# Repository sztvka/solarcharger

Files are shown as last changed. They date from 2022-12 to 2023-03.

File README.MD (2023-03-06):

# SolarCharger
  
This project is my first shot at programming real-time systems featuring multiple tasks. I wanted to create a dual axis solar tracker that's reliable in terms of hardware and software in the field where most of the similar projects run on a breadboard with an Arduino.
The device is able to:
- Track the sun in two axis
- Charge a Lithium-Ion Battery with current limit and overvoltage protection
- Display a web UI with real-time status of the device
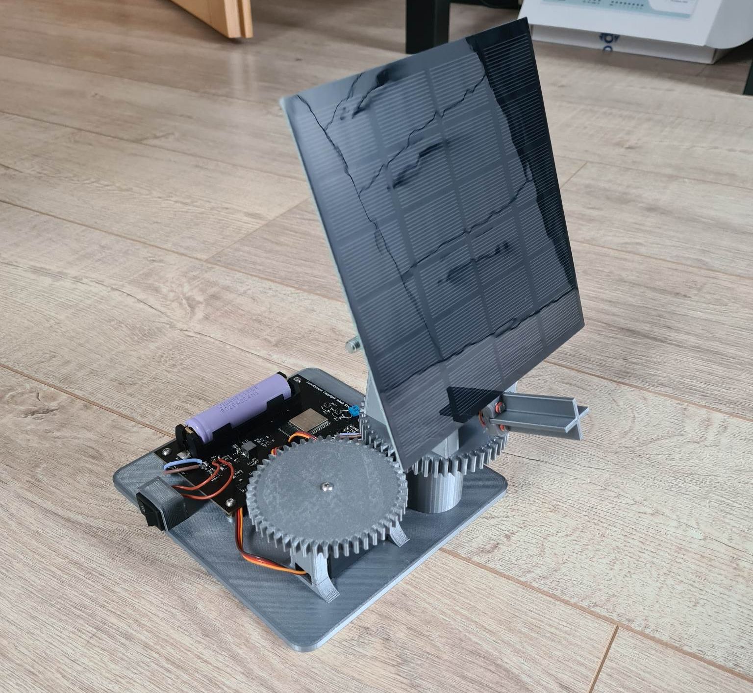
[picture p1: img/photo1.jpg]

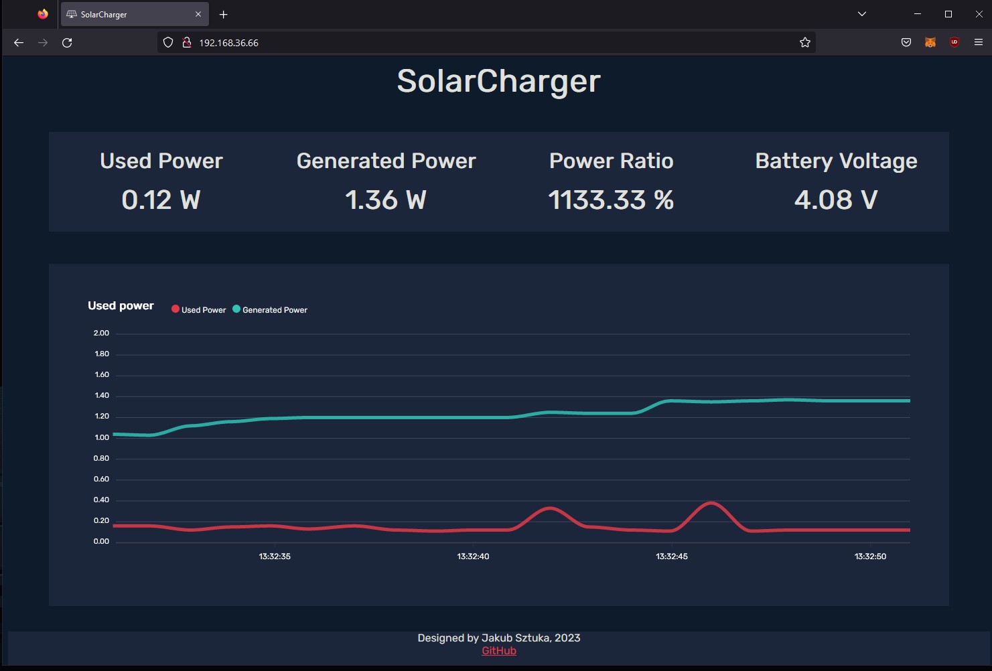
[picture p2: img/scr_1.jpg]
webUI Web UI


## Hardware

### Mechanical
The mechanical design is a remix of the [Dual Axis Solar Tracker](https://www.thingiverse.com/thing:53321) by [OpenSourceClassroom](https://www.thingiverse.com/opensourceclassroom/designs). My updated design fixes some major mechanical issues apparent in the original design, mainly related to poor alignment of the two axis. In my new design, the pan axis is kept aligned with bearings, the gears are screwed on instead of being plastic welded and my design features proper cable management with strain relief.  
Required materials for assembly:
- Printed parts
- M4x10mm Screws
- M4x20mm Screws
- M3x6mm Screws
- 6001 Bearing (I recommend opening it up and removing the grease inside to decrease friction)
- M3 standoffs (Optional, extra space under the pcb allows cable management)
- M6x100mm threaded rod with two M6 nuts
- MG-996R Servo (pan)
- MG90S or SG90 Servo (tilt)
- Cables (silicone insulation is optimal)
- Cable conduit

### Electronics
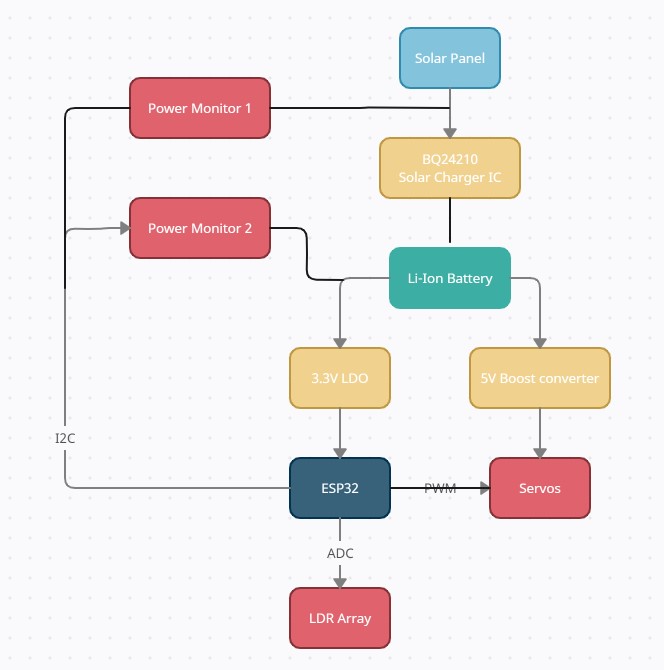
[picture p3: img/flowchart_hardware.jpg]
Hardware flowchart
  
Everything is placed onto a custom pcb. For more details refer to schematics and kicad files in the repository. This design uses a 3W solar panel.

## Software
The code is written in ESP-IDF with FreeRTOS and is designed to run on an ESP32. 

## Compiling

#### Prerequisites
 - [ESP32 Toolchain](https://docs.espressif.com/projects/esp-idf/en/latest/esp32/get-started/index.html#step-2-set-up-the-toolchain)
 - Python interpreter

#### Steps
1. Clone the repository `git clone https://github.com/sztvka/solarcharger.git`
2. Make sure your ESP-IDF path is set correctly and `idf.py` is resolvable
3. Install the required python packages `pip install rjsmin css_html_js_minify`
4. Configure your install in `config_default.h` file
5. Run the `compile_extras.py` script to setup the web UI (this will minify web files and set your config for compiling)
6. Run `idf.py build` to compile the project
7. Flash the device with `idf.py -p (PORT) flash`

## Extra media



https://user-images.githubusercontent.com/47701797/213793889-40177bec-c784-479d-9bc1-420ded0e9b07.mp4

## License

This project is licensed under the Creative Commons Attribution Share Alike 4.0 International - see the [LICENSE](LICENSE) file for details  
cc

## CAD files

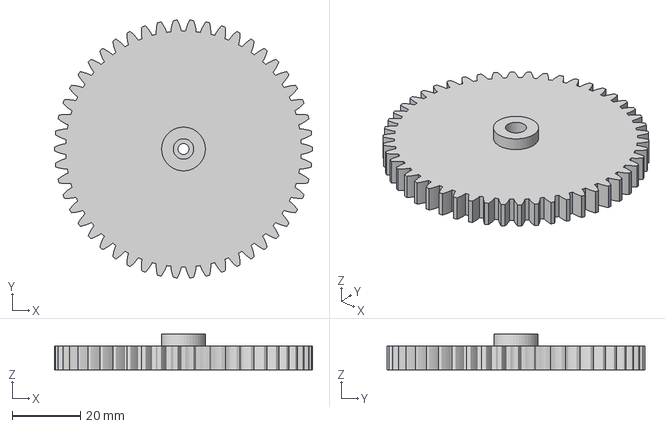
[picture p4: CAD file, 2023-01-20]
3d_models/Pan Gear.3mf
75.4 x 75.3 x 10.5 mm

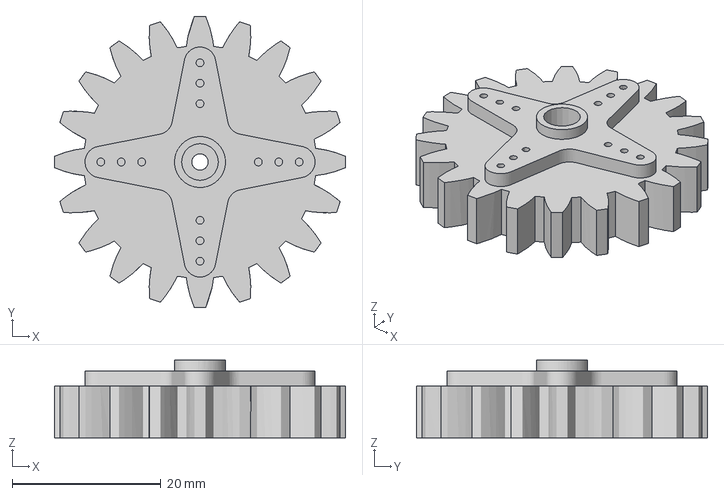
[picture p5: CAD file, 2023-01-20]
3d_models/Tilt Gear.3mf
39.2 x 39.2 x 10.5 mm

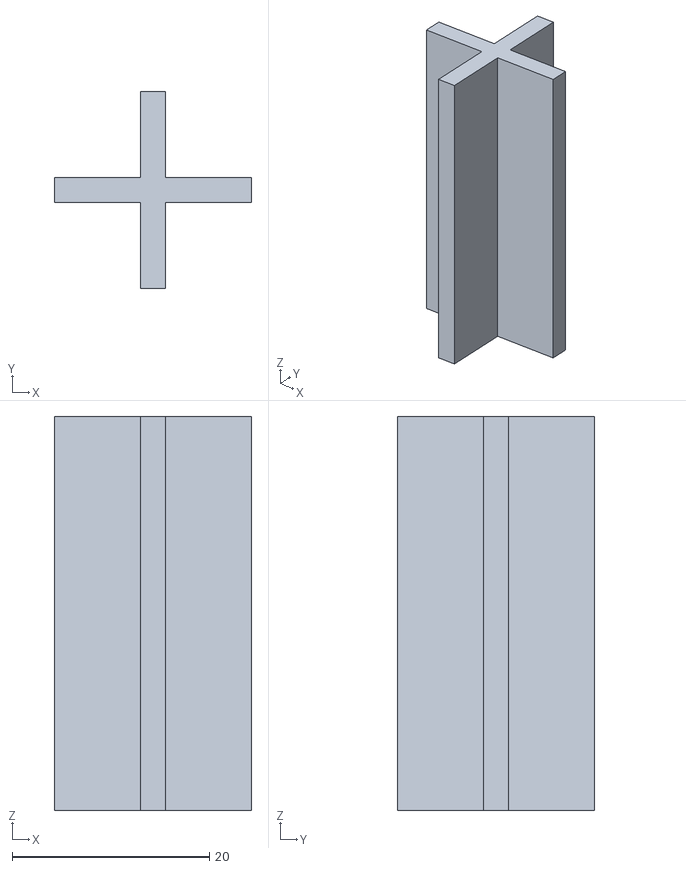
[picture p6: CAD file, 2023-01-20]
3d_models/LDR_Divider.stl
20.0 x 20.0 x 40.0

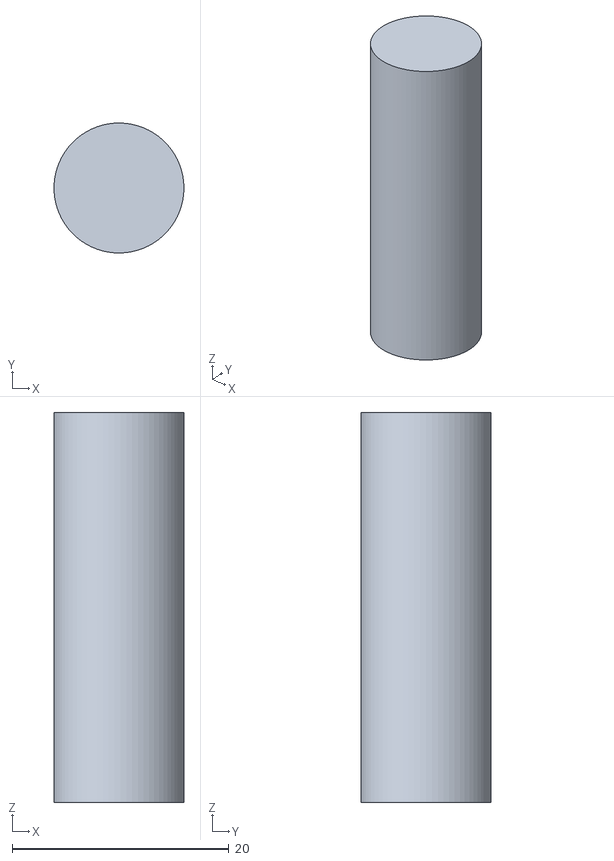
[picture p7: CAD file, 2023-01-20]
3d_models/Base_Gear_Shaft.stl
12.0 x 12.0 x 36.0

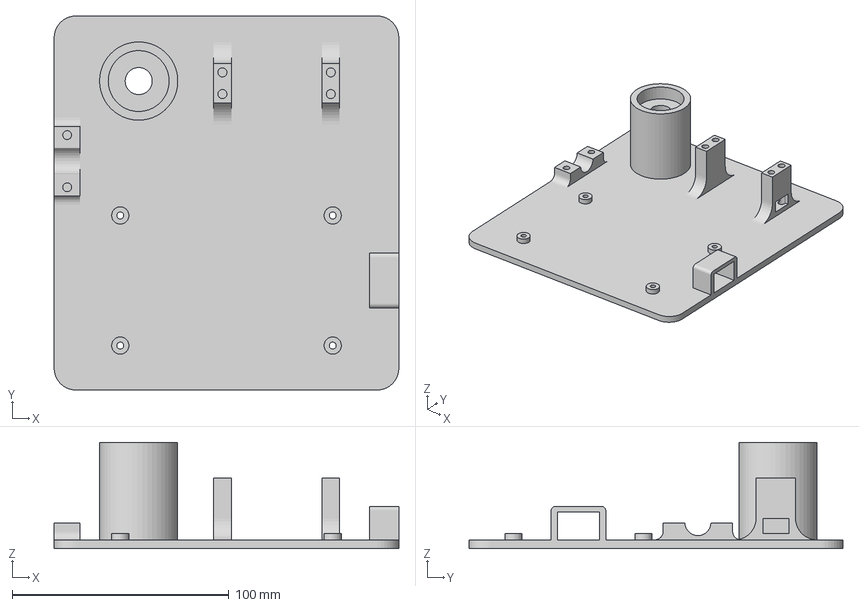
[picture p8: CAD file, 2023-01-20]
3d_models/Base.3mf
159.0 x 172.5 x 49.0 mm

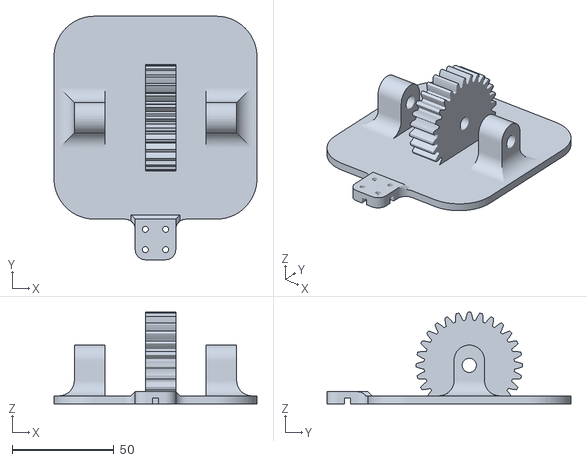
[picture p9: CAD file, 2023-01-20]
3d_models/Panel_Bracket.stl
100.0 x 120.0 x 45.2

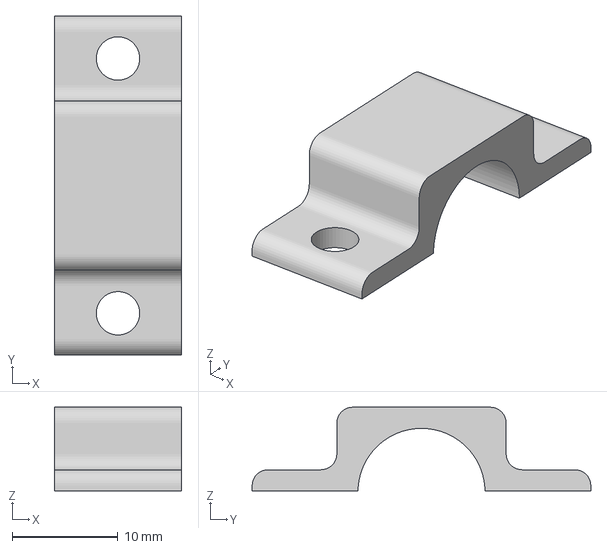
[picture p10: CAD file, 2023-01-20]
3d_models/Cable clip.3mf
12.0 x 32.0 x 7.90 mm

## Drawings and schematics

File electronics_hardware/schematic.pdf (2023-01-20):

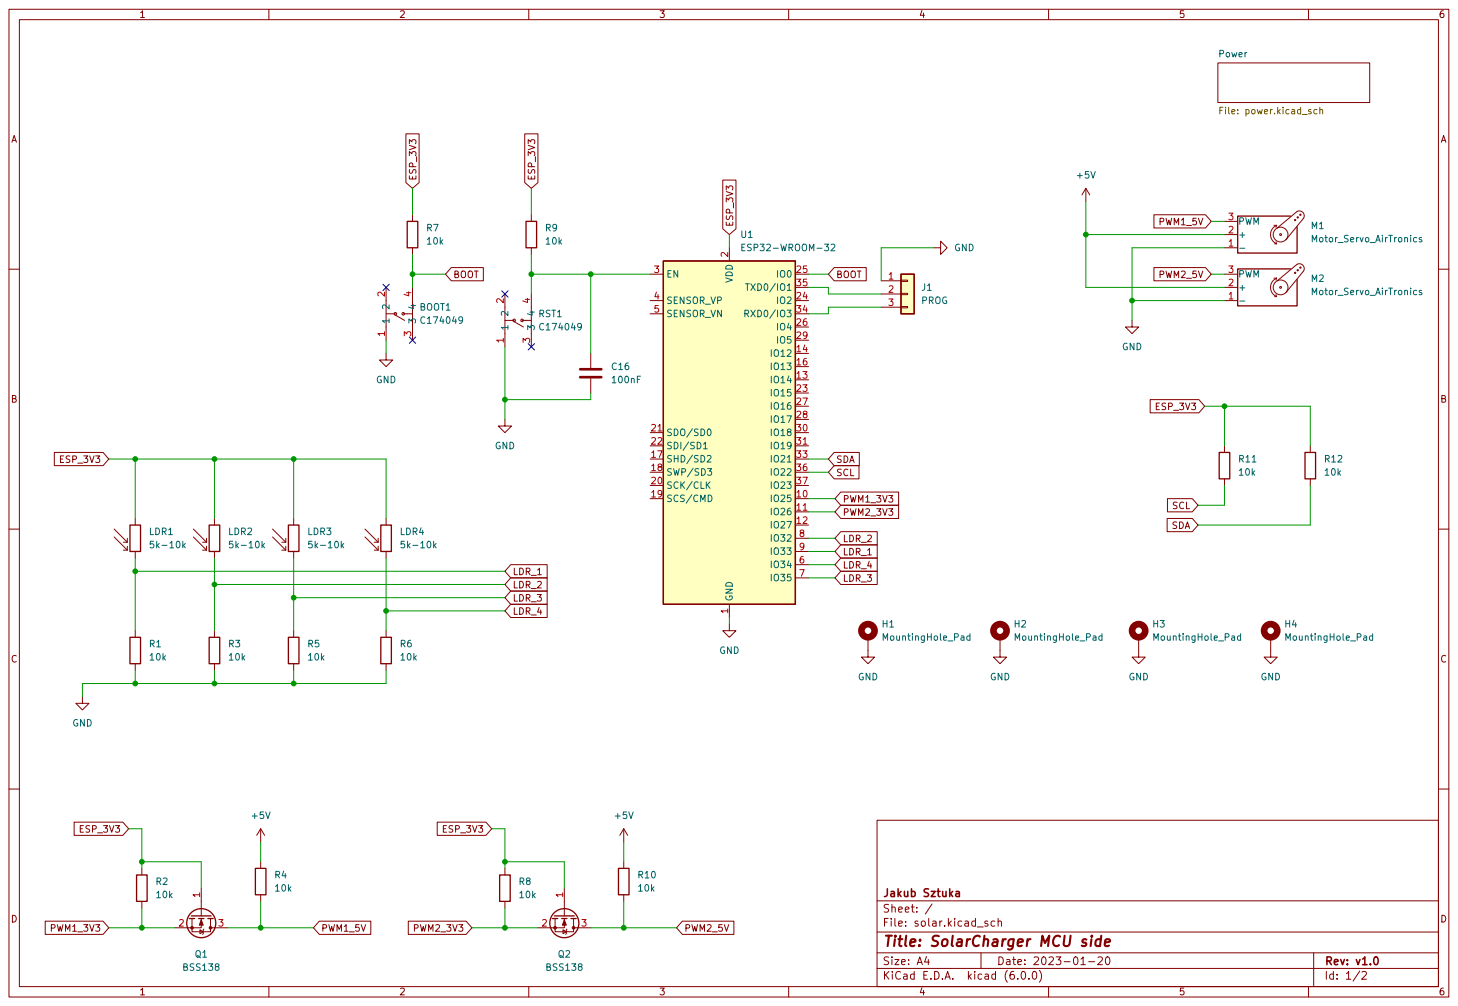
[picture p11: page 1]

2 SCK/CLK 20 SDO/SD0 21 SDI/SD1 22

File: solar.kicad_sch Sheet: / Jakub Sztuka

Id: 1/2 Title: SolarCharger MCU side

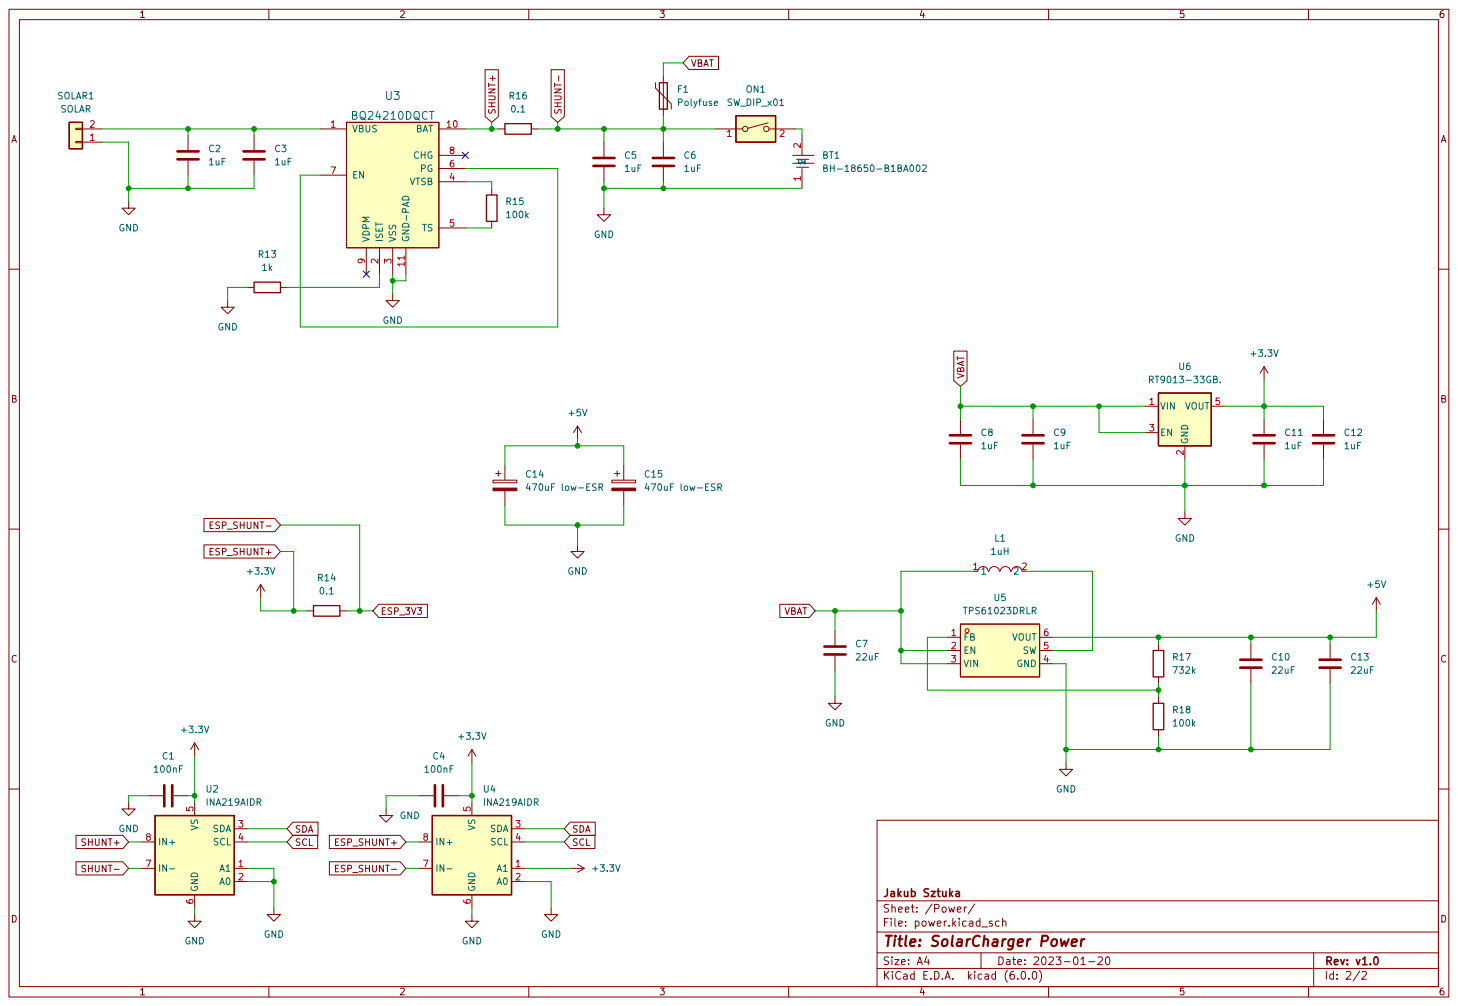
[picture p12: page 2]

3 VTSB 4 TS 5 PG 6 EN 7 CHG 8 VDPM

File: power.kicad_sch Sheet: /Power/ Jakub Sztuka GND

Id: 2/2 Title: SolarCharger Power

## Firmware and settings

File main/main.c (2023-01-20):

#include <sys/cdefs.h>
#include <stdio.h>
#include <freertos/FreeRTOS.h>
#include <freertos/task.h>
#include <ina219.h>
#include <string.h>
#include <esp_log.h>
#include <assert.h>
#include <wifi.h>
#include <iot_servo.h>
#include "driver/adc.h" //deprecated change in the future
#include "esp_adc_cal.h"


#define I2C_PORT 0

#define I2C_SCL 22
#define I2C_SDA 21


// LDR1 33  top left
// LDR2 32  top right
// LDR3 35  bottom left
// LDR4 34  bottom right


#define LDR1 ADC_CHANNEL_4
#define LDR2 ADC_CHANNEL_5
#define LDR3 ADC_CHANNEL_6
#define LDR4 ADC_CHANNEL_7

#define ADC_SAMPLE_SIZE 64

static const adc_bits_width_t width = ADC_WIDTH_BIT_12;
static esp_adc_cal_characteristics_t *ldr_adc_chars;

#define SERVO_1 25
#define SERVO_2 26

#define LDR_DIFF_MOVE_TRESHOLD 100

const uint8_t INA219_1_ADDR = 0x40; //solar
const uint8_t INA219_2_ADDR = 0x44; //esp32

int servo1_angle = 90;
int servo2_angle = 179;

#define SHUNT_MOHM 100
#define MAX_CUR 1


servo_config_t servo_cfg = {
    .max_angle = 180,
    .min_width_us = 500,
    .max_width_us = 2500,
    .freq = 50,
    .timer_number = LEDC_TIMER_0,
    .channels = {
        .servo_pin = {
            SERVO_1,
            SERVO_2,
        },
        .ch = {
            LEDC_CHANNEL_0,
            LEDC_CHANNEL_1,
        },
    },
    .channel_number = 2,
} ;



void ina_measure(void *addr)
{
    TaskHandle_t cur = xTaskGetCurrentTaskHandle();
    char * name = pcTaskGetName(cur);
    ina219_t dev;
    memset(&dev, 0, sizeof(ina219_t));
    uint8_t *address = addr;
    assert(SHUNT_MOHM > 0);
    ESP_ERROR_CHECK(ina219_init_desc(&dev, *address, I2C_PORT, I2C_SDA, I2C_SCL));
    ESP_ERROR_CHECK(ina219_init(&dev));
    ESP_ERROR_CHECK(ina219_configure(&dev, INA219_BUS_RANGE_16V, INA219_GAIN_0_125,
            INA219_RES_12BIT_1S, INA219_RES_12BIT_1S, INA219_MODE_CONT_SHUNT_BUS));

    ESP_ERROR_CHECK(ina219_calibrate(&dev, (float)MAX_CUR, (float)SHUNT_MOHM / 1000.0f));

    float bus_voltage, current, power;

    while (1)
    {
        ESP_ERROR_CHECK(ina219_get_bus_voltage(&dev, &bus_voltage));
        ESP_ERROR_CHECK(ina219_get_current(&dev, &current));
        ESP_ERROR_CHECK(ina219_get_power(&dev, &power));


        if(strcmp(name, "INA219_1")==0) setINA219_1(bus_voltage, current*1000, power*1000); 
        if(strcmp(name, "INA219_2")==0) setINA219_2(bus_voltage, current*1000, power*1000); 
        vTaskDelay(pdMS_TO_TICKS(500));
    }
}



//servo 1 prawo lewo
//sevo 2 gora dol
//servo 2 po odwrocie dol gora


//wieksze od 0 ma isc w prawo
void adjustServos(int diff_vert, int diff_hor){
    if(abs(diff_vert)>=LDR_DIFF_MOVE_TRESHOLD){
        if(diff_vert>0 && servo2_angle>89) servo2_angle-=2;
        else if(diff_vert<0 && servo2_angle<179) servo2_angle+=2;
        iot_servo_write_angle(LEDC_LOW_SPEED_MODE, 1, (float)servo2_angle);
    }
    if(abs(diff_hor)>=LDR_DIFF_MOVE_TRESHOLD){
        if(diff_hor>0 && servo1_angle<179) servo1_angle+=2;
        else if(diff_hor<0 && servo1_angle>1) servo1_angle-=2;
        iot_servo_write_angle(LEDC_LOW_SPEED_MODE, 0, (float)servo1_angle);
    }
}


static void check_adc_efuse(void)
{
    if (esp_adc_cal_check_efuse(ESP_ADC_CAL_VAL_EFUSE_TP) == ESP_OK) {
        printf("ADC eFuse Two Point: Supported\n");
    } else {
        printf("ADC eFuse Two Point: NOT supported\n");
    }
    //Check Vref is burned into eFuse
    if (esp_adc_cal_check_efuse(ESP_ADC_CAL_VAL_EFUSE_VREF) == ESP_OK) {
        printf("ADC eFuse Vref: Supported\n");
    } else {
        printf("ADC eFuse Vref: NOT supported\n");
    }
}


static void print_char_val_type(esp_adc_cal_value_t val_type)
{
    if (val_type == ESP_ADC_CAL_VAL_EFUSE_TP) {
        printf("ADC Characterized using Two Point Value\n");
    } else if (val_type == ESP_ADC_CAL_VAL_EFUSE_VREF) {
        printf("ADC Characterized using eFuse Vref\n");
    } else {
        printf("ADC Characterized using Default Vref\n");
    }
}




void ldr_setup(){
    check_adc_efuse();

    adc1_config_width(width);
    adc1_config_channel_atten(LDR1, ADC_ATTEN_DB_11);
    adc1_config_channel_atten(LDR2, ADC_ATTEN_DB_11);
    adc1_config_channel_atten(LDR3, ADC_ATTEN_DB_11);
    adc1_config_channel_atten(LDR4, ADC_ATTEN_DB_11);
    ldr_adc_chars = calloc(1, sizeof(esp_adc_cal_characteristics_t));
    esp_adc_cal_value_t val_type = esp_adc_cal_characterize(ADC_UNIT_1, ADC_ATTEN_DB_11, width, 1100, ldr_adc_chars);
    print_char_val_type(val_type); 
}

_Noreturn void ldr_read(){
    iot_servo_write_angle(LEDC_LOW_SPEED_MODE, 0, (float)servo1_angle);
    iot_servo_write_angle(LEDC_LOW_SPEED_MODE, 1, (float)servo2_angle);
    while(1){
        uint32_t ldr_raw_reading[4] = {0};
        uint32_t ldr_voltage[4] = {0};
        for (int i = 0; i<ADC_SAMPLE_SIZE; i++){
            ldr_raw_reading[0] += adc1_get_raw((adc1_channel_t)LDR1);
            ldr_raw_reading[1] += adc1_get_raw((adc1_channel_t)LDR2);
            ldr_raw_reading[2] += adc1_get_raw((adc1_channel_t)LDR3);
            ldr_raw_reading[3] += adc1_get_raw((adc1_channel_t)LDR4);
        };
        
        for(int i = 0; i<4; i++){
            ldr_raw_reading[i] /= ADC_SAMPLE_SIZE;
            ldr_voltage[i] = esp_adc_cal_raw_to_voltage(ldr_raw_reading[i], ldr_adc_chars);
        };


    int avg_top = (int)(ldr_voltage[0] + ldr_voltage[1]) / 2;
    int avg_bot = (int)(ldr_voltage[2] + ldr_voltage[3]) / 2;
    int avg_left = (int)(ldr_voltage[0] + ldr_voltage[2]) / 2;
    int avg_right = (int)(ldr_voltage[1] + ldr_voltage[3]) / 2;



    int diff_vertical = avg_top-avg_bot; //  positive: top is brighter   negative: bottom is brighter
    int diff_horizontal = avg_left-avg_right; //positive left is brighter   negative right is brighter


   
    adjustServos(diff_vertical, diff_horizontal);
    vTaskDelay(pdMS_TO_TICKS(100));
    }
}


void app_main()
{
    ESP_ERROR_CHECK(i2cdev_init());

    wifi_init();
    setINA219_1(0.1,0.1,0.1);
    setINA219_2(0.2,0.2,0.2);
    xTaskCreate(ina_measure, "INA219_1", configMINIMAL_STACK_SIZE * 8, (void*)&INA219_1_ADDR, 5, NULL);
    xTaskCreate(ina_measure, "INA219_2", configMINIMAL_STACK_SIZE * 8, (void*)&INA219_2_ADDR, 5, NULL);
    iot_servo_init(LEDC_LOW_SPEED_MODE, &servo_cfg);
    ldr_setup();
    xTaskCreate(ldr_read, "ADC", configMINIMAL_STACK_SIZE*8, NULL, 4, NULL);

}

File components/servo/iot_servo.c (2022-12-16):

// Copyright 2020 Espressif Systems (Shanghai) Co. Ltd.
//
// Licensed under the Apache License, Version 2.0 (the "License");
// you may not use this file except in compliance with the License.
// You may obtain a copy of the License at
//
//     http://www.apache.org/licenses/LICENSE-2.0
//
// Unless required by applicable law or agreed to in writing, software
// distributed under the License is distributed on an "AS IS" BASIS,
// WITHOUT WARRANTIES OR CONDITIONS OF ANY KIND, either express or implied.
// See the License for the specific language governing permissions and
// limitations under the License.

#include "esp_log.h"
#include "esp_err.h"
#include "driver/ledc.h"
#include "iot_servo.h"
#include <config.h>

#define SERVO_CHECK(a, str, ret_val) \
    if (!(a)) { \
        ESP_LOGE(TAG,"%s(%d): %s", __FUNCTION__, __LINE__, str); \
        return (ret_val); \
    }

#define SERVO_LEDC_INIT_BITS LEDC_TIMER_10_BIT
#define SERVO_FREQ_MIN       50
#define SERVO_FREQ_MAX       400

static uint32_t g_full_duty = 0;
static servo_config_t g_cfg[LEDC_SPEED_MODE_MAX] = {0};

static uint32_t calculate_duty(ledc_mode_t speed_mode, float angle)
{
    float angle_us = angle / g_cfg[speed_mode].max_angle * (g_cfg[speed_mode].max_width_us - g_cfg[speed_mode].min_width_us) + g_cfg[speed_mode].min_width_us;
    ESP_LOGD(TAG, "angle us: %f", angle_us);
    uint32_t duty = (uint32_t)((float)g_full_duty * (angle_us) * g_cfg[speed_mode].freq / (1000000.0f));
    return duty;
}

static float calculate_angle(ledc_mode_t speed_mode, uint32_t duty)
{
    float angle_us = (float)duty * 1000000.0f / (float)g_full_duty / (float)g_cfg[speed_mode].freq;
    angle_us -= g_cfg[speed_mode].min_width_us;
    angle_us = angle_us < 0.0f ? 0.0f : angle_us;
    float angle = angle_us * g_cfg[speed_mode].max_angle / (g_cfg[speed_mode].max_width_us - g_cfg[speed_mode].min_width_us);
    return angle;
}

esp_err_t iot_servo_init(ledc_mode_t speed_mode, const servo_config_t *config)
{
    esp_err_t ret;
    SERVO_CHECK(NULL != config, "Pointer of config is invalid", ESP_ERR_INVALID_ARG);
    SERVO_CHECK(config->channel_number > 0 && config->channel_number <= LEDC_CHANNEL_MAX, "Servo channel number out the range", ESP_ERR_INVALID_ARG);
    SERVO_CHECK(config->freq <= SERVO_FREQ_MAX && config->freq >= SERVO_FREQ_MIN, "Servo pwm frequency out the range", ESP_ERR_INVALID_ARG);
    uint64_t pin_mask = 0;
    uint32_t ch_mask = 0;
    for (size_t i = 0; i < config->channel_number; i++) {
        uint64_t _pin_mask = 1ULL << config->channels.servo_pin[i];
        uint32_t _ch_mask = 1UL << config->channels.ch[i];
        SERVO_CHECK(!(pin_mask & _pin_mask), "servo gpio has a duplicate", ESP_ERR_INVALID_ARG);
        SERVO_CHECK(!(ch_mask & _ch_mask), "servo channel has a duplicate", ESP_ERR_INVALID_ARG);
        SERVO_CHECK(GPIO_IS_VALID_OUTPUT_GPIO(config->channels.servo_pin[i]), "servo gpio invalid", ESP_ERR_INVALID_ARG);
        pin_mask |= _pin_mask;
        ch_mask |= _ch_mask;
    }

    ledc_timer_config_t ledc_timer = {
        .clk_cfg = LEDC_AUTO_CLK,
        .duty_resolution = SERVO_LEDC_INIT_BITS,     // resolution of PWM duty
        .freq_hz = config->freq,                     // frequency of PWM signal
        .speed_mode = speed_mode,            // timer mode
        .timer_num = config->timer_number            // timer index
    };
    ret = ledc_timer_config(&ledc_timer);
    SERVO_CHECK(ESP_OK == ret, "ledc timer configuration failed", ESP_FAIL);
    for (size_t i = 0; i < config->channel_number; i++) {
        ledc_channel_config_t ledc_ch = {
            .intr_type  = LEDC_INTR_DISABLE,
            .channel    = config->channels.ch[i],
            .duty       = calculate_duty(speed_mode, 0),
            .gpio_num   = config->channels.servo_pin[i],
            .speed_mode = speed_mode,
            .timer_sel  = config->timer_number,
            .hpoint     = 0
        };
        ret = ledc_channel_config(&ledc_ch);
        SERVO_CHECK(ESP_OK == ret, "ledc channel configuration failed", ESP_FAIL);
    }
    g_full_duty = (1 << SERVO_LEDC_INIT_BITS) - 1;
    g_cfg[speed_mode] = *config;

    return ESP_OK;
}

esp_err_t iot_servo_deinit(ledc_mode_t speed_mode)
{
    SERVO_CHECK(speed_mode < LEDC_SPEED_MODE_MAX, "LEDC speed mode invalid", ESP_ERR_INVALID_ARG);
    for (size_t i = 0; i < g_cfg[speed_mode].channel_number; i++) {
        ledc_stop(speed_mode, g_cfg[speed_mode].channels.ch[i], 0);
    }
    ledc_timer_rst(speed_mode, g_cfg[speed_mode].timer_number);
    g_full_duty = 0;
    return ESP_OK;
}

esp_err_t iot_servo_write_angle(ledc_mode_t speed_mode, uint8_t channel, float angle)
{
    SERVO_CHECK(speed_mode < LEDC_SPEED_MODE_MAX, "LEDC speed mode invalid", ESP_ERR_INVALID_ARG);
    SERVO_CHECK(channel < LEDC_CHANNEL_MAX, "LEDC channel number too large", ESP_ERR_INVALID_ARG);
    SERVO_CHECK(angle >= 0.0f, "Angle can't to be negative", ESP_ERR_INVALID_ARG);
    esp_err_t ret;
    uint32_t duty = calculate_duty(speed_mode, angle);
    ret = ledc_set_duty(speed_mode, (ledc_channel_t)channel, duty);
    ret |= ledc_update_duty(speed_mode, (ledc_channel_t)channel);
    SERVO_CHECK(ESP_OK == ret, "write servo angle failed", ESP_FAIL);
    return ESP_OK;
}

esp_err_t iot_servo_read_angle(ledc_mode_t speed_mode, uint8_t channel, float *angle)
{
    SERVO_CHECK(speed_mode < LEDC_SPEED_MODE_MAX, "LEDC speed mode invalid", ESP_ERR_INVALID_ARG);
    SERVO_CHECK(channel < LEDC_CHANNEL_MAX, "LEDC channel number too large", ESP_ERR_INVALID_ARG);
    uint32_t duty = ledc_get_duty(speed_mode, channel);
    float a = calculate_angle(speed_mode, duty);
    *angle = a;
    return ESP_OK;
}

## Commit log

2022-11-30 spiffs alpha feature
    [partitions.csv]
2022-12-23 adc ldr readout and servo prep
2023-01-19 readme init and minor fixes
    [main.c]
2023-01-20 readme update and 3d models
    [Base.3mf, Base_Gear_Shaft.stl, Cable clip.3mf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]
2023-01-20 readme update and schematic add
2023-01-21 schematic update include BOM
